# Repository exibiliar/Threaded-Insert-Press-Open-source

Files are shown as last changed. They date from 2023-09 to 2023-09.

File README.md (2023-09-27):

# Threaded Insert Press Open-source
<p align="center">
    This is a Threaded Insert Press created 70% from 3d printed parts and with as few components as possible.
    <br/>
    <br/>
  
  </p>
</p>

## Let's Build It

### Prerequisites

Before you start assembling the press you will need the following 
- 1X m5 nut wrench
- 1X M5 allen wrench
- The components you find inside the BOM
- Scissors or something to cut the belt

### Step 1
As the first thing you need **"Base.stl"** then **"2040 V Slot Extrusion 400mm"** and as the last thing 2X **"M5 x 30 Button head"**
<br>
<br>
 

### Step 2
Screw **"Base.stl"** with **"2040 V Slot Extrusion 400mm"**
<br>
<br>
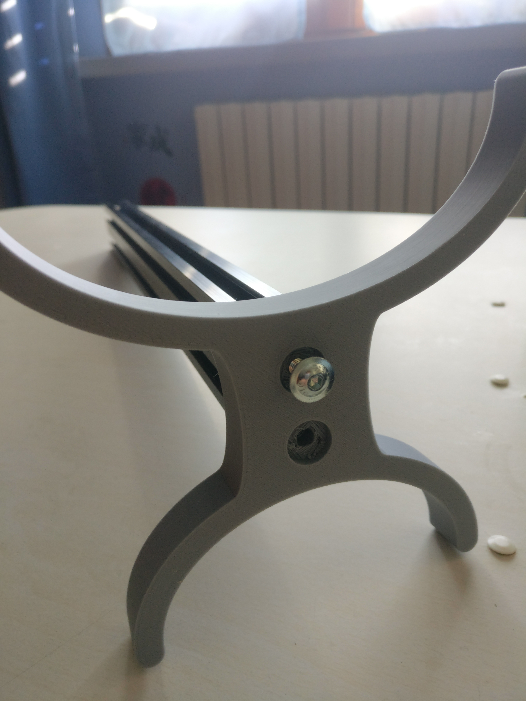
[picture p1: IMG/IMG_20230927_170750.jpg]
 

### Step 3
The components we need to assemble the front carriage are. 

- 7X **M5 x 30 Button head**
- 7X **M5 Nut**
- 3X **608RS Bearings**
- 3X **Bearings Out.stl**
- 3X **Bearings In.stl**
- 3X **Spacer.stl**
- 1X **Decentration Post .stl**
- 1X **Front Carriage.stl**
- 1X **Soldering Arm.stl**
- 1X **Soldering Iron Grip Standard .stl** or **Soldering Iron Grip.stl**

Please check before installing **Soldering Iron Grip** if your tin soldering iron is compatible 
<br>
<br>
 

### Step 4
Install **Bearings In.stl** over **M5 x 30 Button head** and Press **Bearings Out.stl** over **608RS Bearings**
<br>
<br>
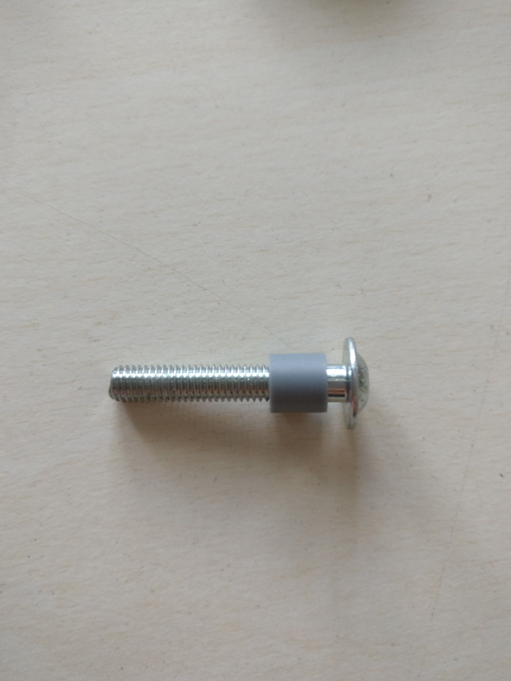
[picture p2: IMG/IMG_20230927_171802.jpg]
 

### Step 5
Now combine the two parts and do it twice more
<br>
<br>
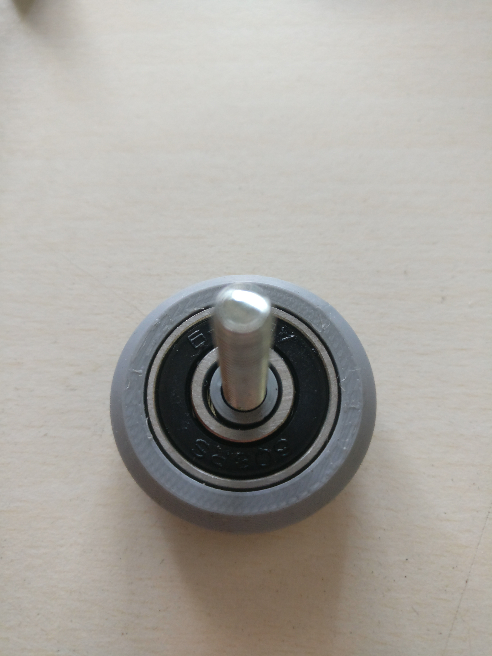
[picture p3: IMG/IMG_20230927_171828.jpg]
 

### Step 6
Now put **Spacer.stl** on top of two bearings as in the image
<br>
<br>
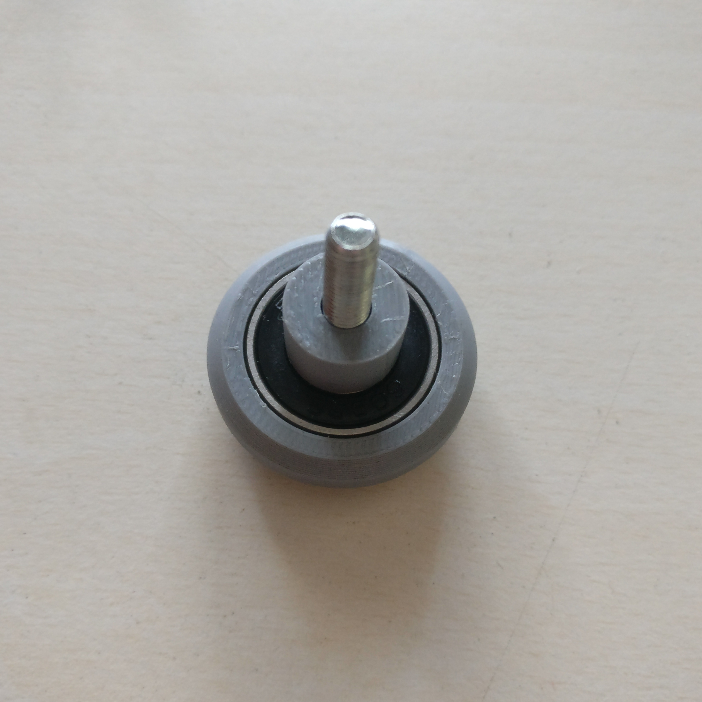
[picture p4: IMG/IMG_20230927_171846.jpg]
 

### Step 7
Put **Decentration Post .stl** above the last bolt
<br>
<br>
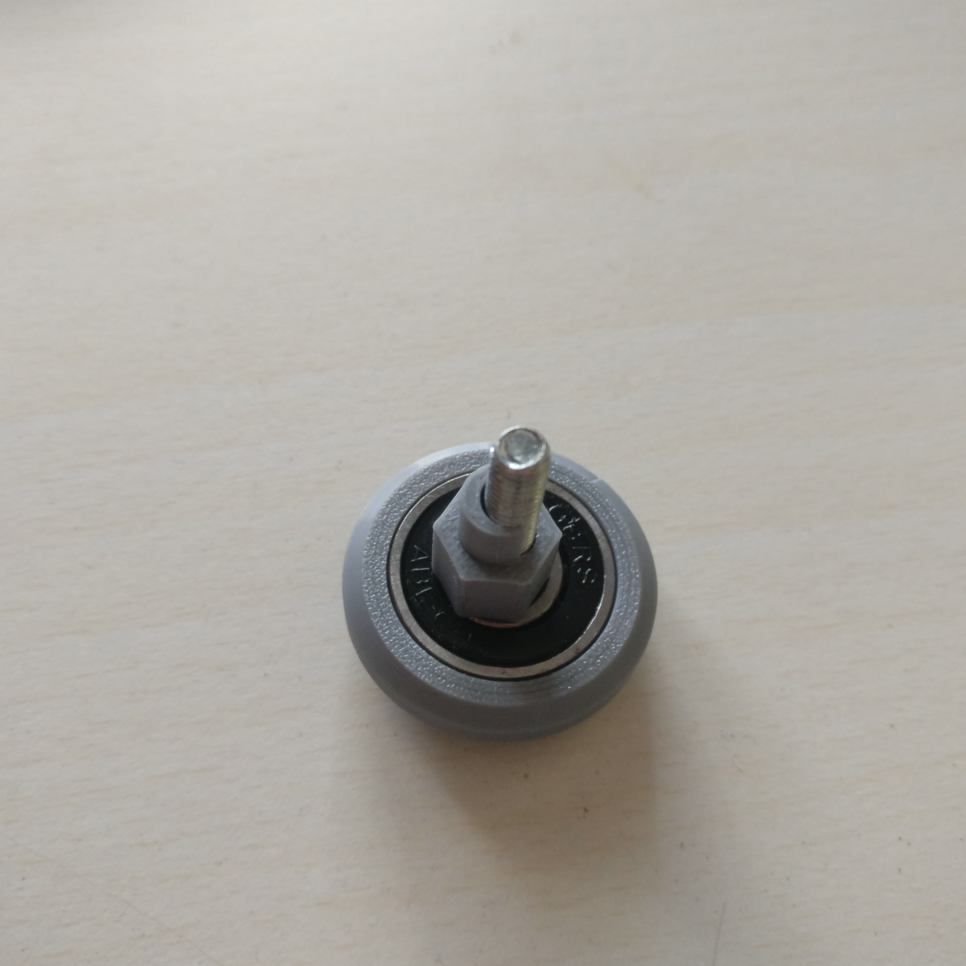
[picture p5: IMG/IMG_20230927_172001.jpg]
 

 ### Step 8
Now install everything on **Front Carriage.stl** and pay attention to the orientation of the part, the bearings should be on the inside of the front carriage to be sure if the bearings are facing upwards the **FRONT** should be upside down
<br>
<br>
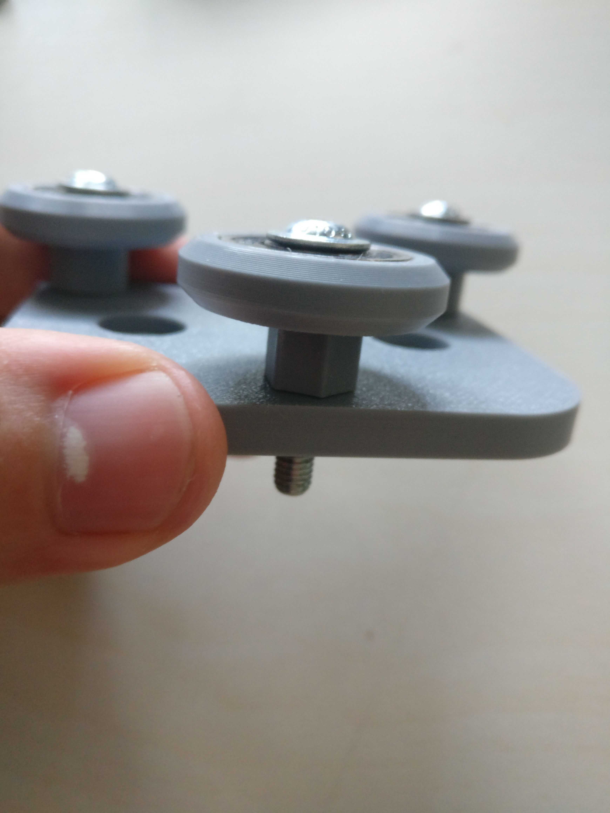
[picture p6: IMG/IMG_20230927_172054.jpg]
 

### Step 9
Now place two screws inside **Soldering Iron Grip.Stl**.
<br>
<br>
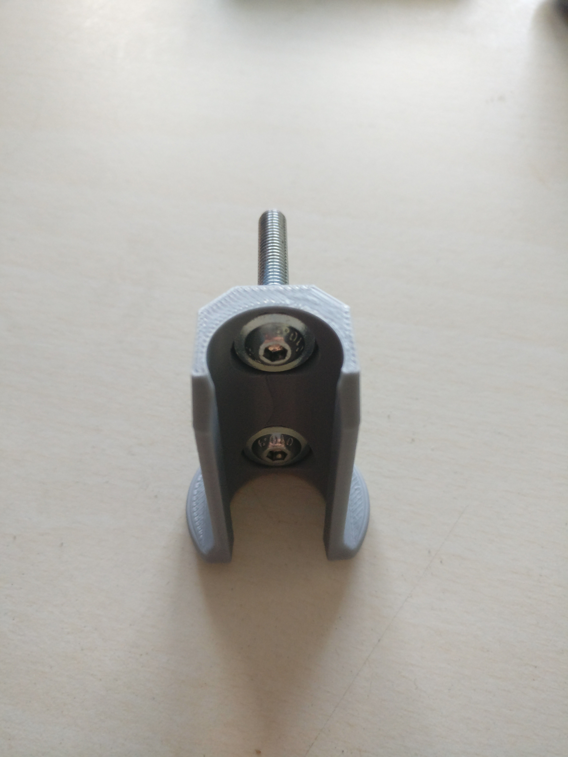
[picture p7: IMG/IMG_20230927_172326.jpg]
 

### Step 10
Now house two bolts inside **Soldering Arm.stl** and screw it together with **Soldering Iron Grip.stl**.
<br>
<br>
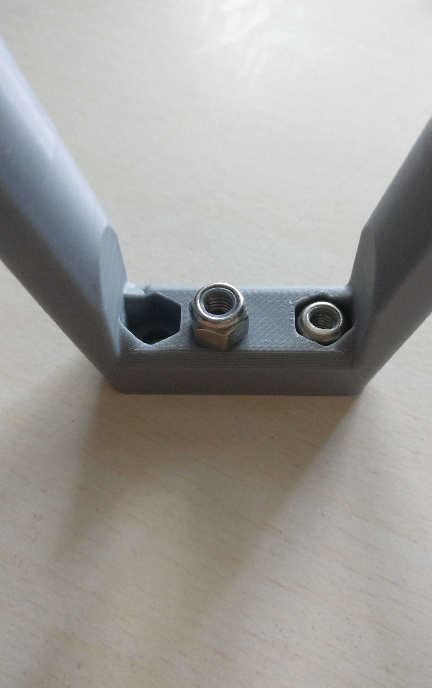
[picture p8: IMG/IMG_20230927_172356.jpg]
 

 ### Step 11
Once this is done we are ready to assemble the two parts together 
<br>
<br>
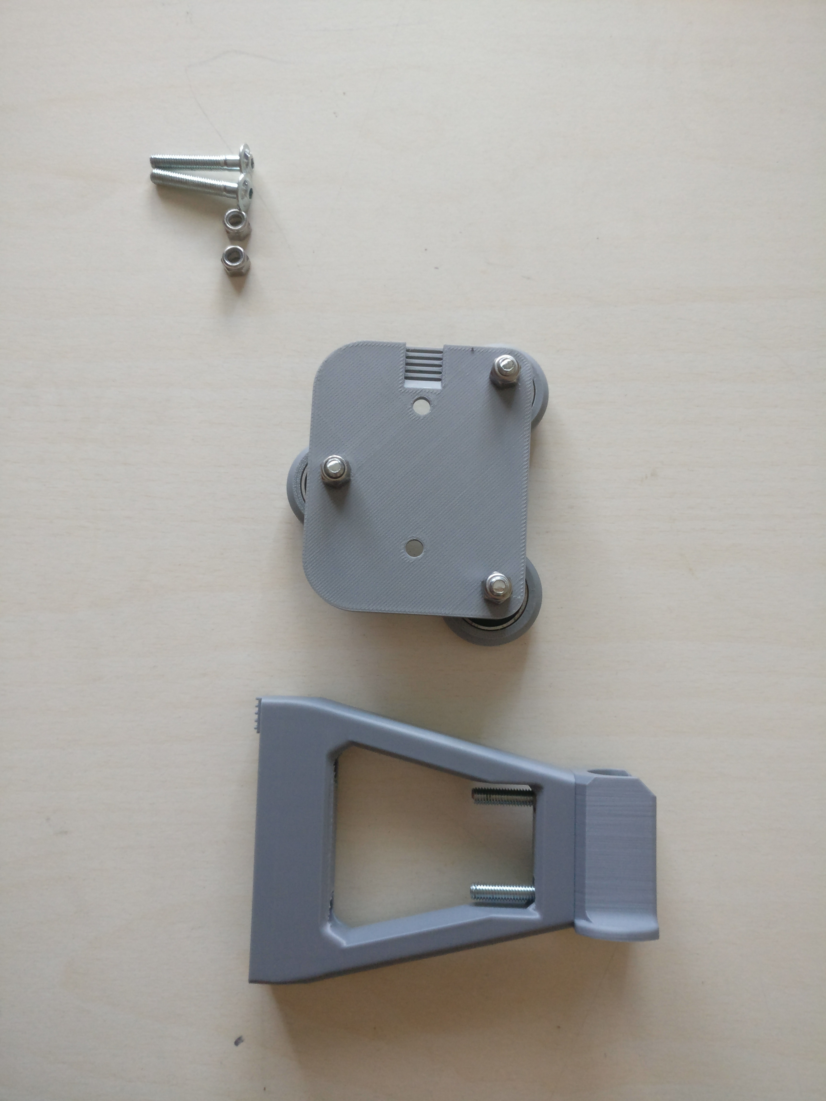
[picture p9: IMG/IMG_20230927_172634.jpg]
 

 ### Step 12
Place one end of the belt inside **Base.stl** facing inward with the grooves and place over **Soldering Arm** and screw it on like the other side
<br>
<br>
 

 ### Step 13
Repeat the same process also for **Rear Carriage .stl**, now we need other coponents which are

- 10X **Washers**
- 3X **M5 Nut**
- 1X **Cover.stl**
- 1X **Weight Arm.stl**

<br>
<br>
 

 ### Step 14
Now cut the belt to 45cm in length and install the newly cut end on **Rear Carriage .stl** with the clamping done by **Weight Arm.stl** and install an **M5 Nut** for added security 
<br>
<br>
 

  ### Step 15
Put washers over the screws (it may take more or less depending on your soldering iron) 
<br>
<br>
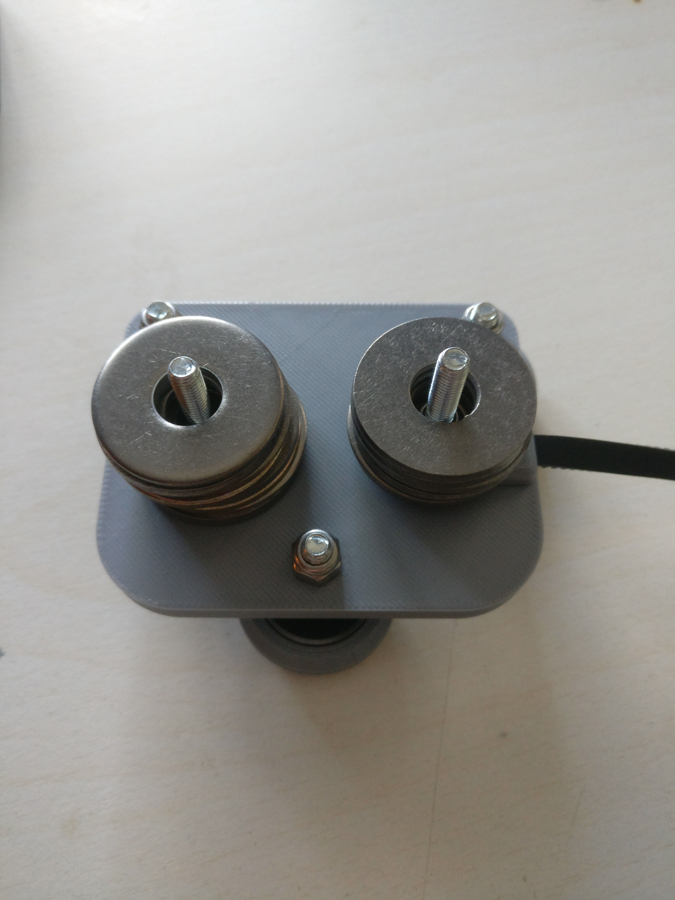
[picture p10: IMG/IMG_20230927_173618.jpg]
 

  ### Step 16
Now put **Cover.stl** above **Rear Carriage**.
<br>
<br>
 

  ### Step 17
Tighten everything with two nuts
<br>
<br>
 

  ### Step 18
This should be the result so far
<br>
<br>
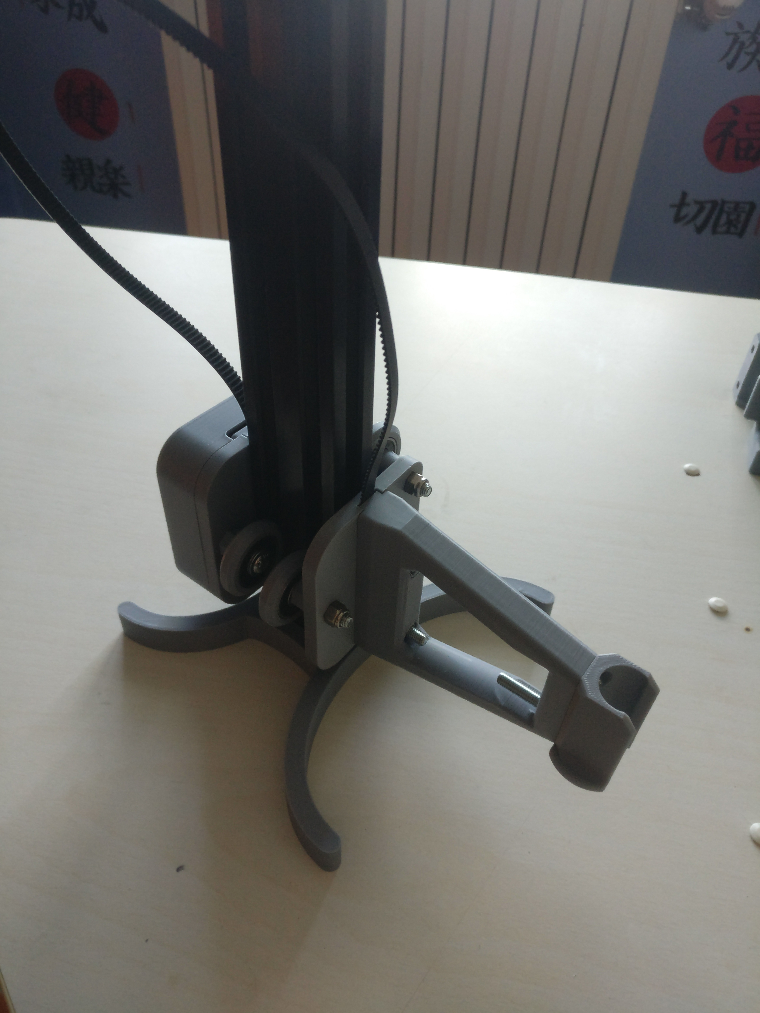
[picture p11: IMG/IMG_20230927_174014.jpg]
 

### Step 19
Now we go to press over the last two **Bearings H.stl** bearings and immediately install **Pulley Plate .stl** on **2040 V Slot Extrusion 400mm** with two screws, once this is done we can install as done previously the bearings and check that the carriages slide well 
<br>
<br>
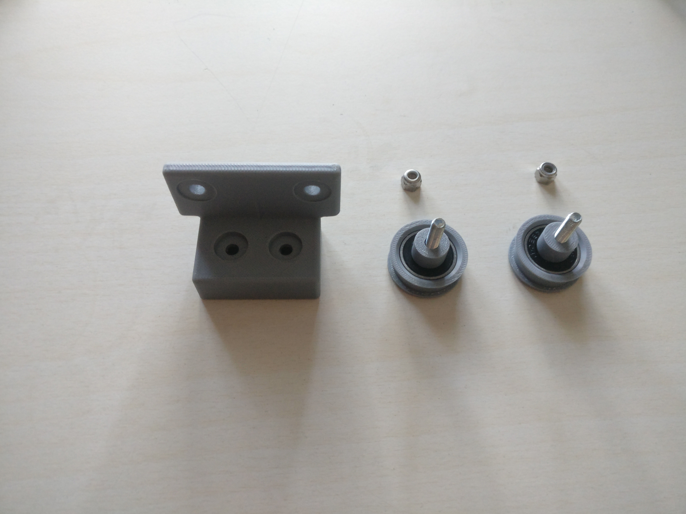
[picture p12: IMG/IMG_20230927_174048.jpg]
 

 ### Step 20
Now that you have finished installing everything rotate the **Decentration Post .stl** to keep the two carriages from jolting, if the belt should not be totally straight just loosen the nuts a bit and fix it 
<br>
<br>

## License

Distributed under the MIT License. See [LICENSE](https://github.com/Exibiliar/Threaded-Insert-Press-Open-source/blob/main/LICENSE.md) for more information.

## Authors

* **Exibiliar** - *Just a tipical nerd* - [Exibiliar](https://github.com/exibiliar) - **

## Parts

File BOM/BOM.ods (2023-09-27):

Category | Part | Quantity | Est Cost | Total | €73.20
Fixings | M5 Nut | 16 | €0.20 | €3.20
Fixings | Washers | 7 | €0.20 | €1.40
Fixings | M5 x 30 Button head | 16 | €0.25 | €4.00
Mechanical | 2040 V Slot Extrusion 400mm | 1 | €22.00 | €22.00
Mechanical | 6mm 2GT Belt approx 410mm | 1 | €10.00 | €10.00
Mechanical | 608RS Bearings | 8 | €0.20 | €1.60
Other | Soldering Iron | 1 | €12.00 | €12.00
Other | Heat Insert Tip | 1 | €19.00 | €19.00

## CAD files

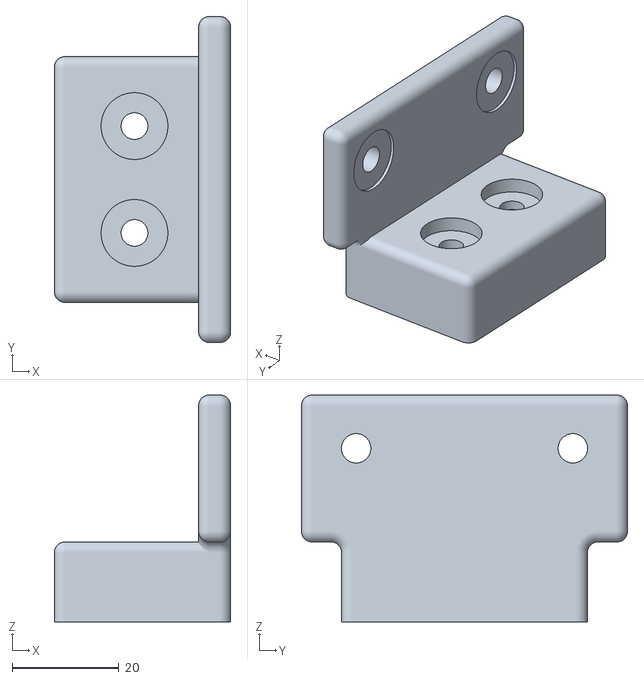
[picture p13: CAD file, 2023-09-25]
STL/Pulley Plate .stl
33.0 x 61.0 x 42.5

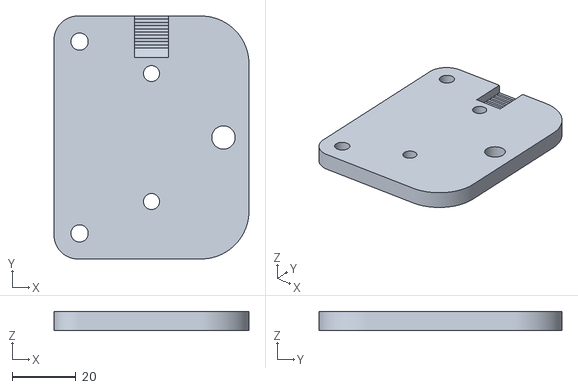
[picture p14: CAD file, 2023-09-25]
STL/Rear Carriage .stl
61.0 x 76.0 x 6.00

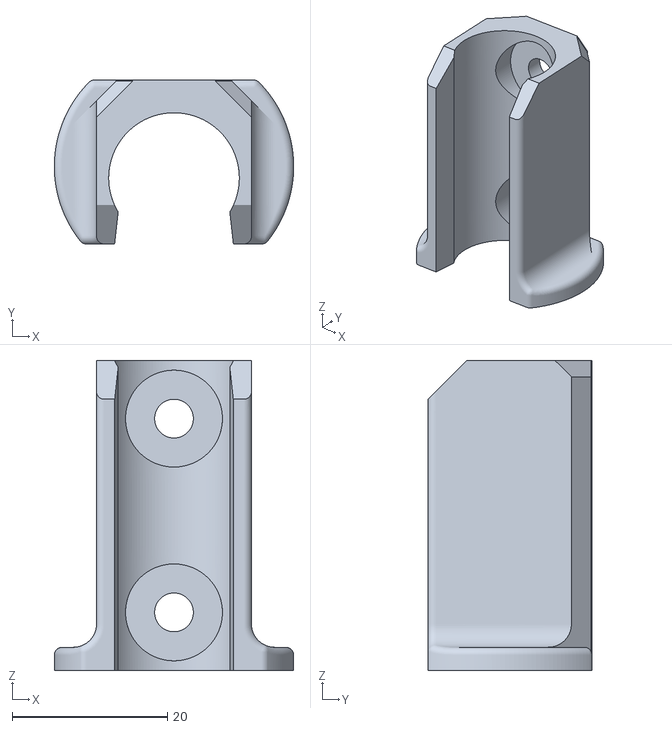
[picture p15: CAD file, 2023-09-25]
STL/Soldering Iron Grip Standard .stl
30.9 x 21.1 x 40.0

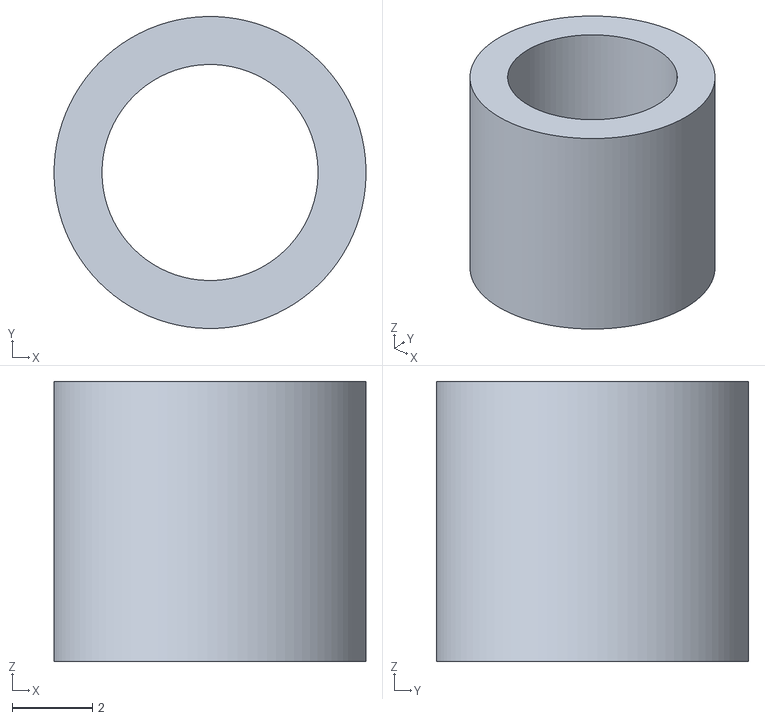
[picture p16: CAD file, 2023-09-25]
STL/Bearings In.stl
7.80 x 7.80 x 7.00

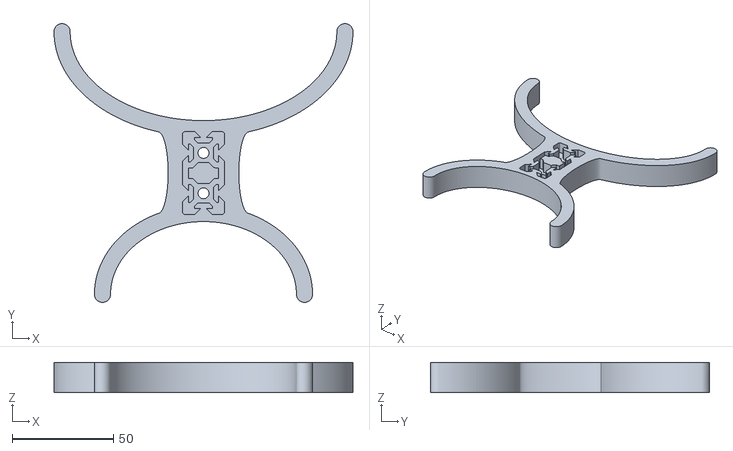
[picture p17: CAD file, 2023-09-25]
STL/Base.stl
148.0 x 138.0 x 15.0

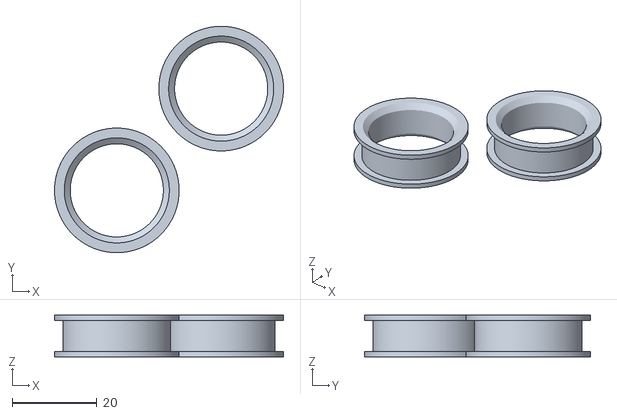
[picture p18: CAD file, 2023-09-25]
STL/Bearings H.stl
54.1 x 53.5 x 9.82

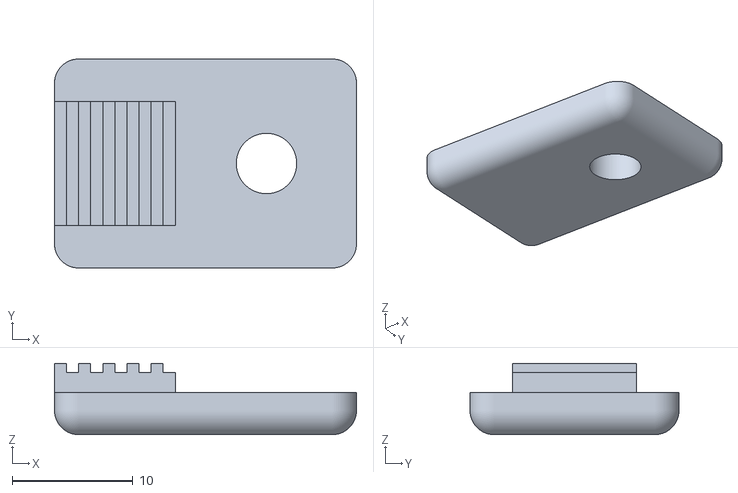
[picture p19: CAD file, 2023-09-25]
STL/Weight Arm.stl
25.0 x 17.3 x 5.90

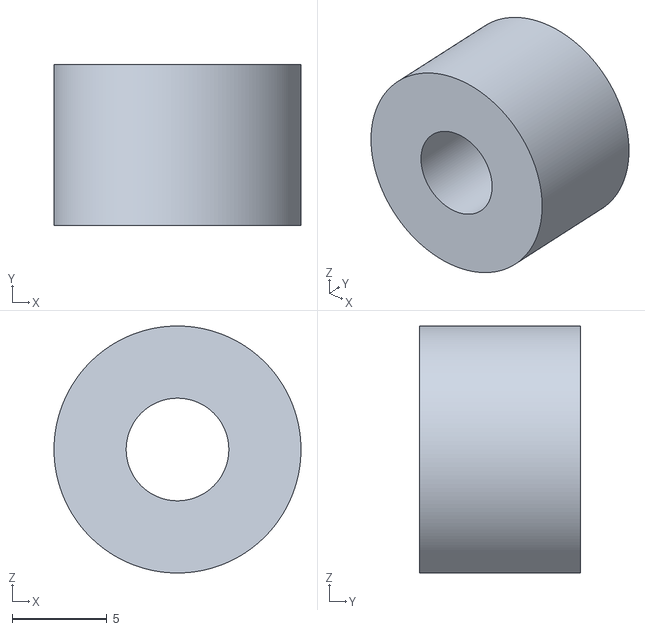
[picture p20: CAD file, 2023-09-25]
STL/Spacer.stl
13.0 x 8.45 x 13.0

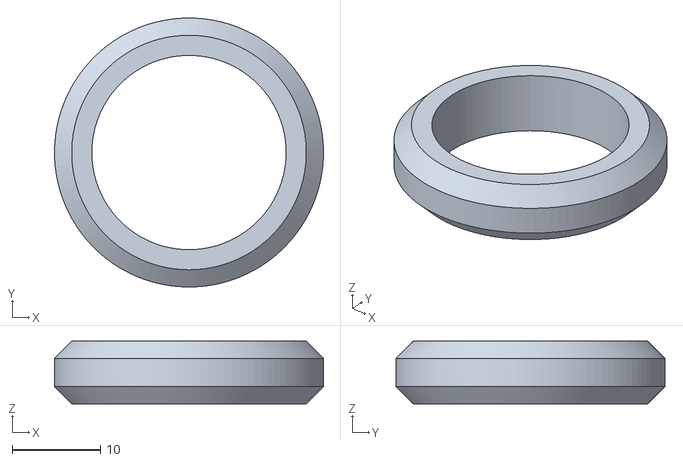
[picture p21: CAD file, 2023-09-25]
STL/Bearings Out.stl
30.5 x 30.5 x 7.09

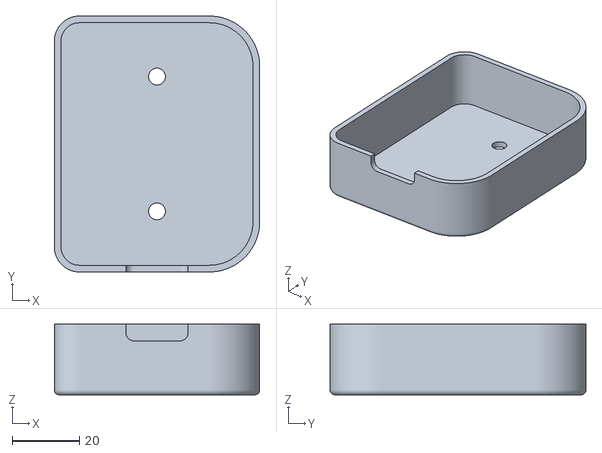
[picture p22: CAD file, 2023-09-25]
STL/Cover.stl
61.0 x 76.0 x 21.0

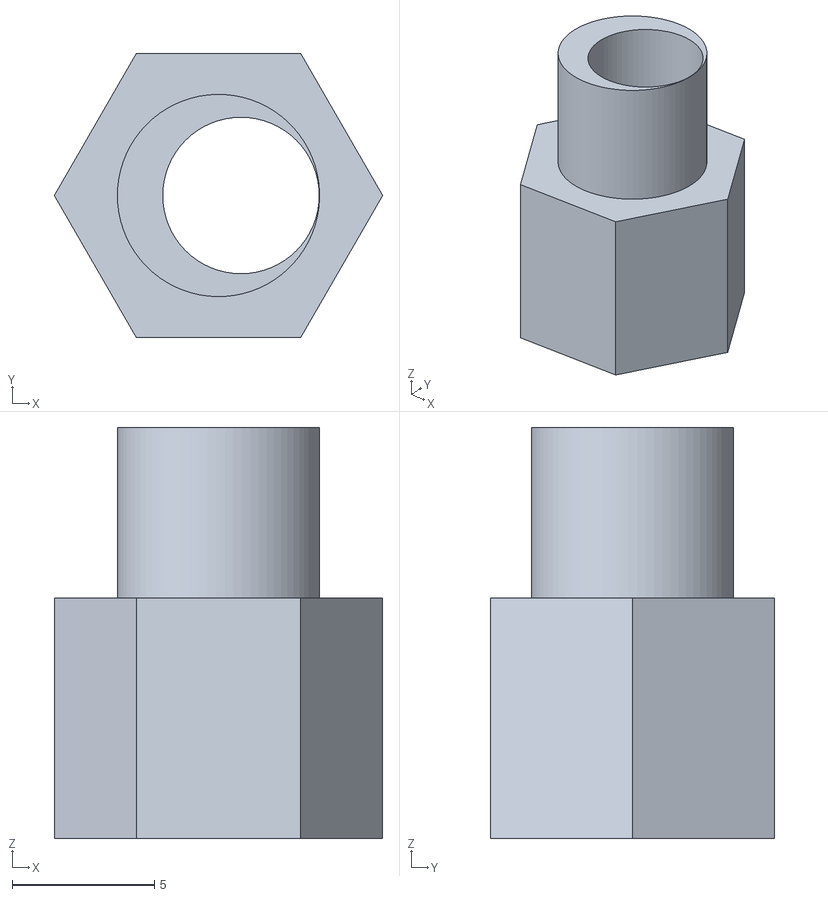
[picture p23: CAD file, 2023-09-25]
STL/Decentration Post .stl
11.5 x 10.0 x 14.5

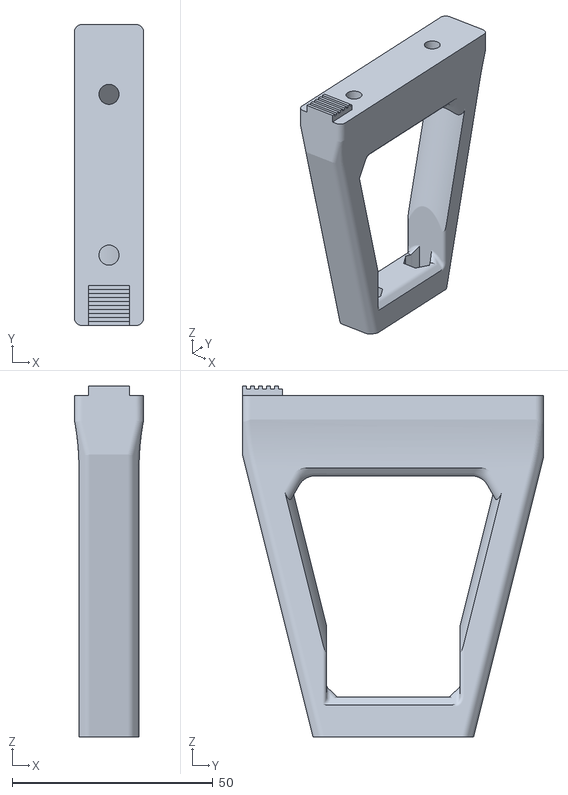
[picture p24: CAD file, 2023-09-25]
STL/Soldering Arm.stl
17.3 x 75.0 x 87.4

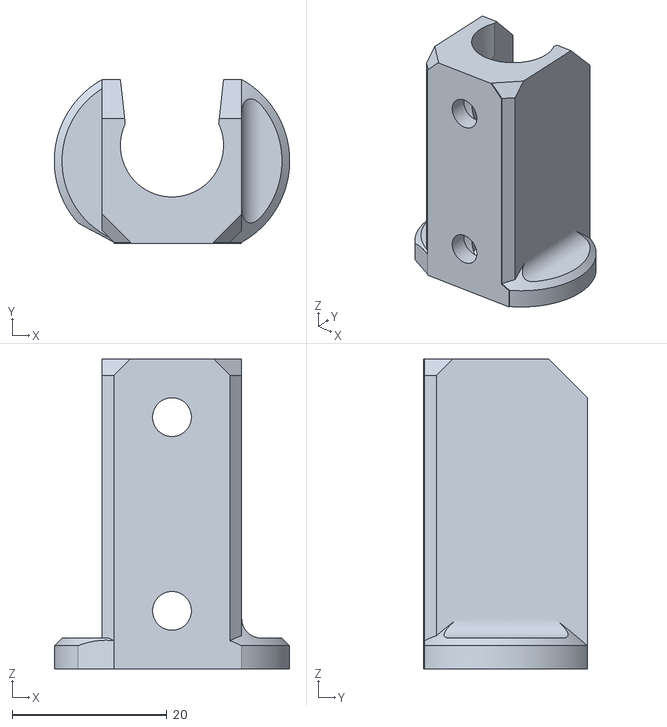
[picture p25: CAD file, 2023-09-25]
STL/Soldering Iron Grip.stl
30.4 x 21.1 x 40.0

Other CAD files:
STL/Front Carriage.stl
